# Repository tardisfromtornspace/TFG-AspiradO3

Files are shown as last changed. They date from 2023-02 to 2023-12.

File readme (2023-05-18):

Proyecto AspiradO3

Nuestro sistema está propuesto para limpiar la troposfera de sustancias químicas nocivas, principalmente el ozono troposférico, pero con unas simples modificaciones también de otros agentes contaminantes como el óxido nitroso, monóxido de carbono y partículas en suspensión, de acuerdo a las ODS 2 (Salud) y 13 (Acción por el clima).
Para ello, según nuestro plan inicial, utilizaríamos un sistema similar a un dirigible o globo aerostático, en el que los sistemas de control y actuación de nuestro dron estarían suspendidos por un globo de un gas ligero, helio o hidrógeno. Esto es para poder llegar a las áreas donde el ozono troposférico se encuentre, y donde un simple filtro a nivel del suelo no pudiera ayudar. El concepto funcionaría de forma similar a una aspiradora, en la que un motor propulsa el aire a través de una serie de filtros que eliminan el gas contaminante, utilizando un filtro de carbón activo, más un par de filtros anti-pájaro y HVAC (no está de más limpiar un poco la atmósfera de polución, ni evitar que nuestro filtro para ozono reaccione con otras sustancias no deseadas), y posiblemente un filtro catabólico selectivo de NOX basado en urea.

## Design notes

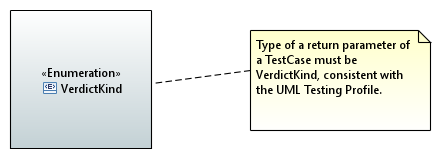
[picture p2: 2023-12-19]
Auxiliar/Papyrus/Test/Requirements_VerdictKind_Diagram.PNG

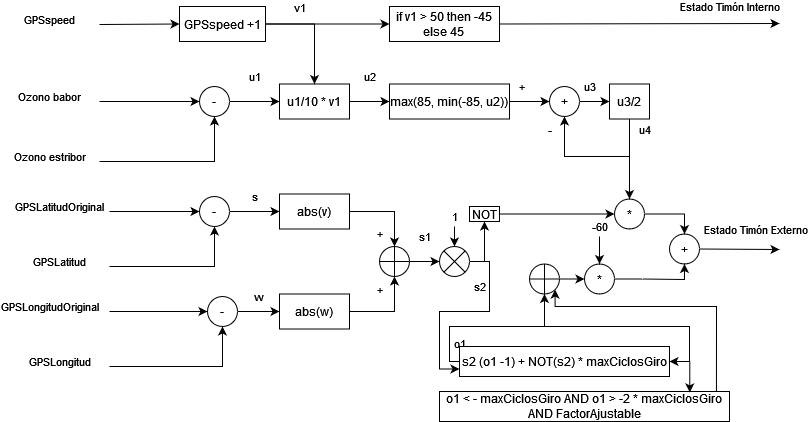
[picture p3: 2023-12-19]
Auxiliar/DiagramaSistemaControlSimple.png

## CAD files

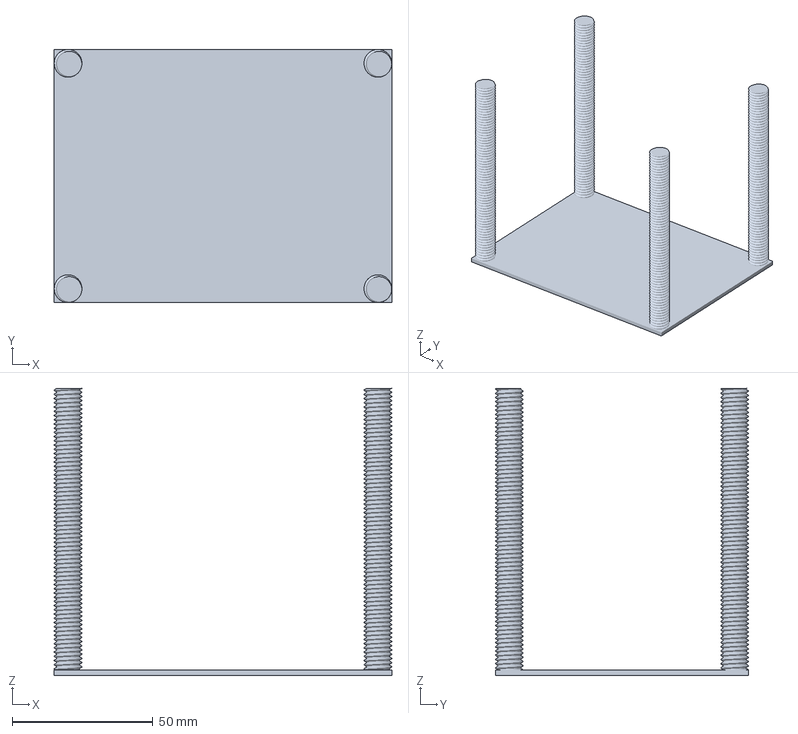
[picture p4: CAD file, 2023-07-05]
Chasis3D/main_structure.3mf
120.0 x 90.0 x 102.0 mm

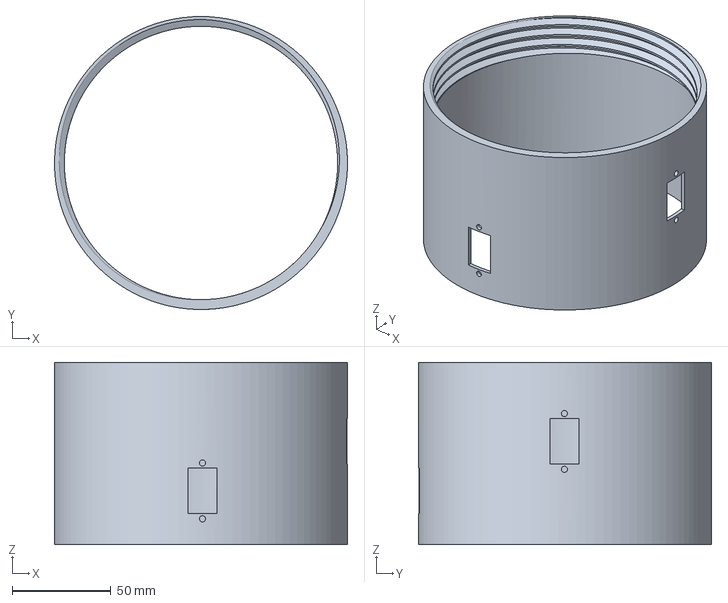
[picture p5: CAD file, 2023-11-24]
Chasis3D/CE3E3V2_tapa-trasera.3mf
148.0 x 148.0 x 92.0 mm

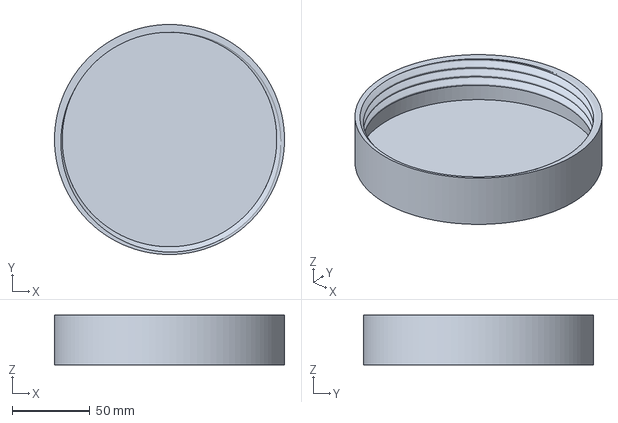
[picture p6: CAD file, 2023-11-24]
Chasis3D/CE3E3V2_tapas1y2.3mf
148.0 x 148.0 x 32.0 mm

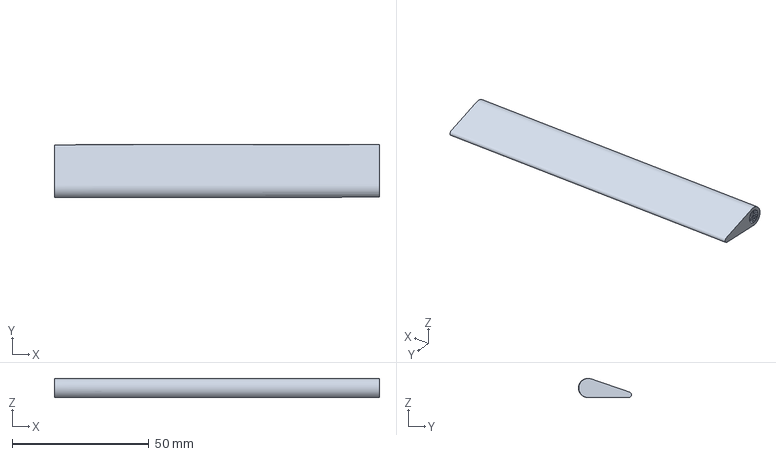
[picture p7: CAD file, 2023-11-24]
Chasis3D/CE3E3V2_timon_2.3mf
118.8 x 19.4 x 7.04 mm

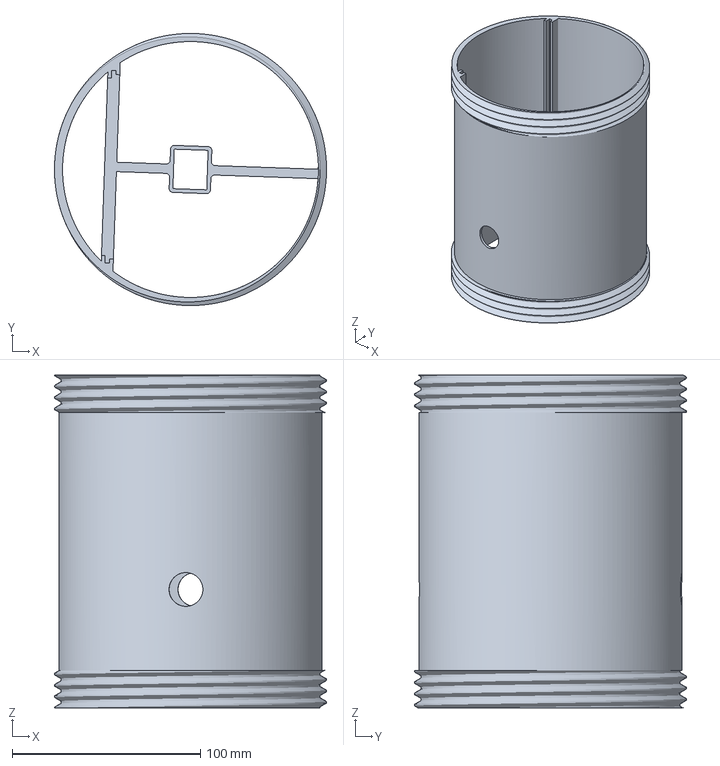
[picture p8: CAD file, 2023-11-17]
Chasis3D/CE3E3V2_chasis.3mf
144.6 x 144.6 x 177.0 mm

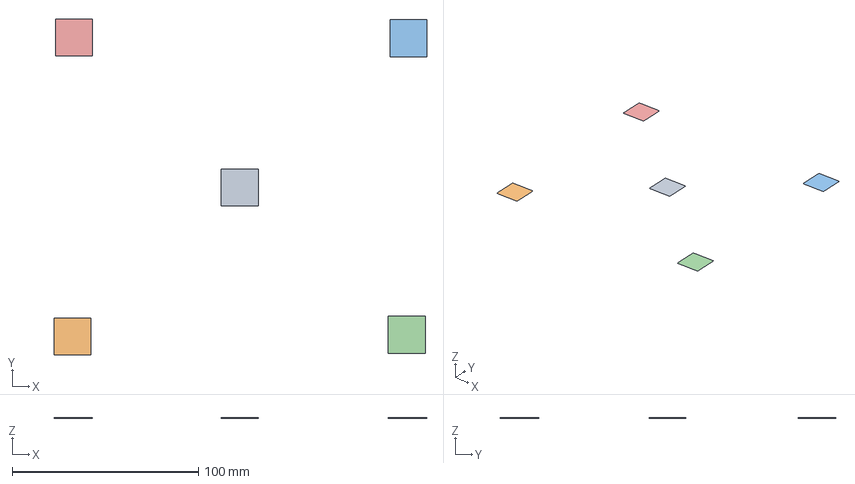
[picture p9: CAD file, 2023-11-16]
Chasis3D/CE3E3V2_Unnamed-Cubo5-PruebaEnder.3mf
200.3 x 180.4 x 0.4 mm
Unnamed-Cubo-PruebaEnder.stl
Unnamed-Cubo-PruebaEnder.stl(1)
Unnamed-Cubo-PruebaEnder.stl(2)
Unnamed-Cubo-PruebaEnder.stl(3)
Unnamed-Cubo-PruebaEnder.stl(4)

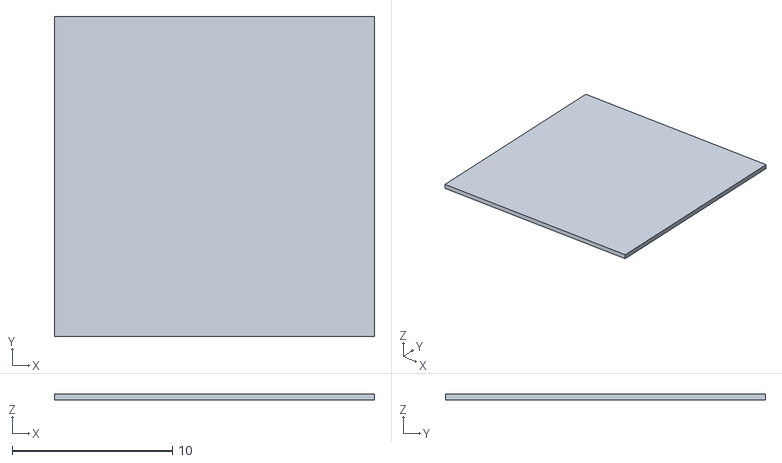
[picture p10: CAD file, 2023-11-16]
Chasis3D/Unnamed-Cubo-PruebaEnder.stl
20.0 x 20.0 x 0.4

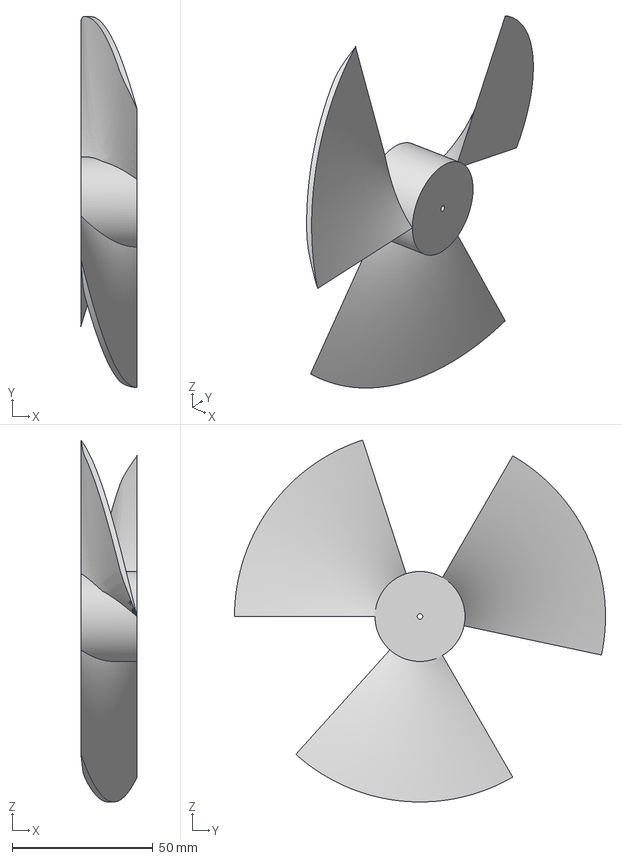
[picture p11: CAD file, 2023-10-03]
Chasis3D/helize.3mf
20.0 x 132.0 x 128.8 mm

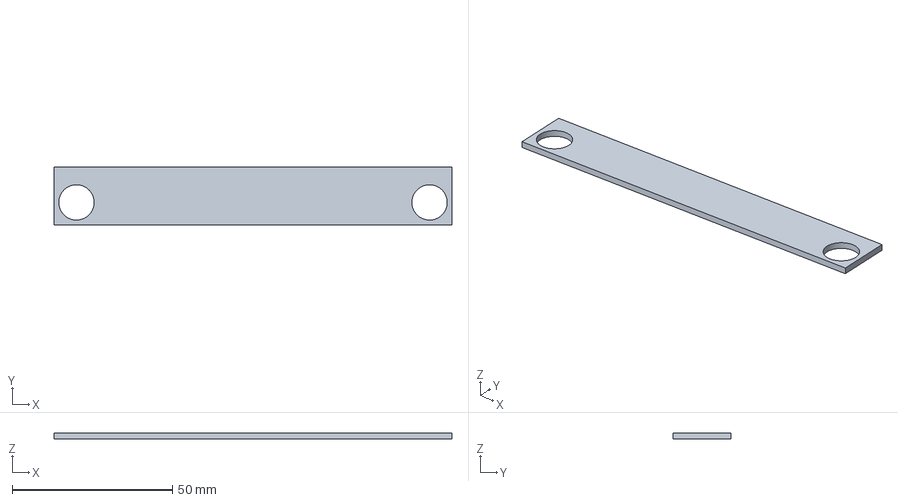
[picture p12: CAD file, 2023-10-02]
Chasis3D/ASX1_Cuerpo17AbrazaderasSoporte.3mf
124.0 x 18.0 x 2.00 mm

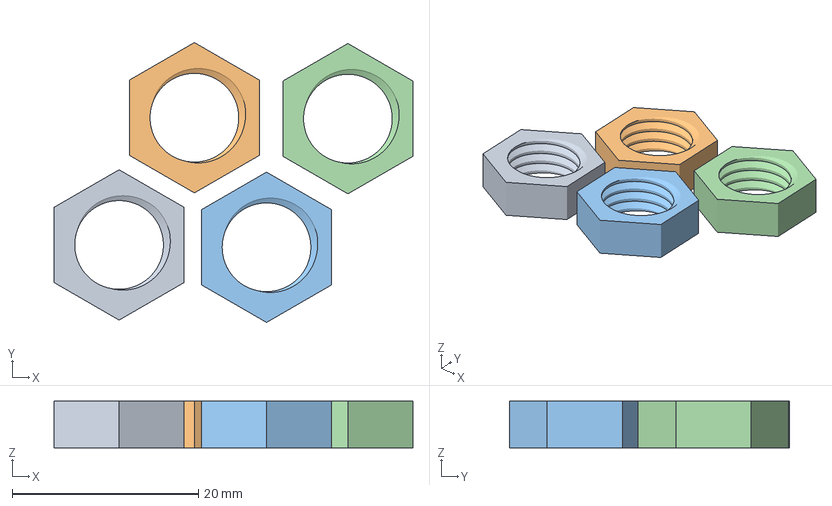
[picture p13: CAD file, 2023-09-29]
Chasis3D/These_nuts_4.3mf
38.6 x 30.1 x 5.00 mm
nut.3mf
nut.3mf(1)
nut.3mf(2)
nut.3mf(3)

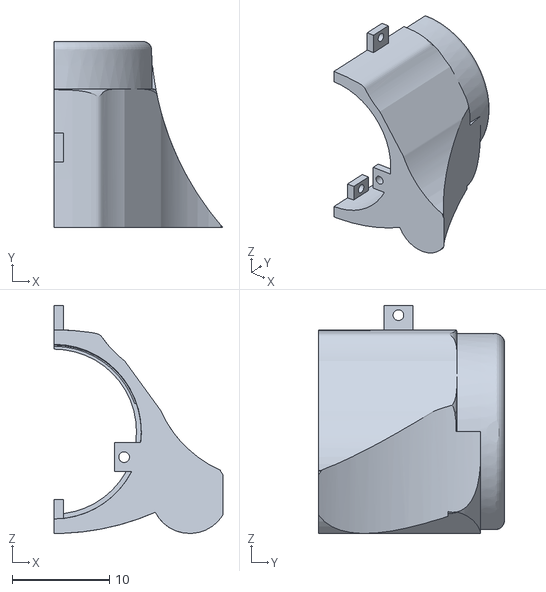
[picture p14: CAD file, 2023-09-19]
Chasis3D/ChasisBI_v3pto2-PROPUESTA.stl
17.4 x 19.2 x 23.5

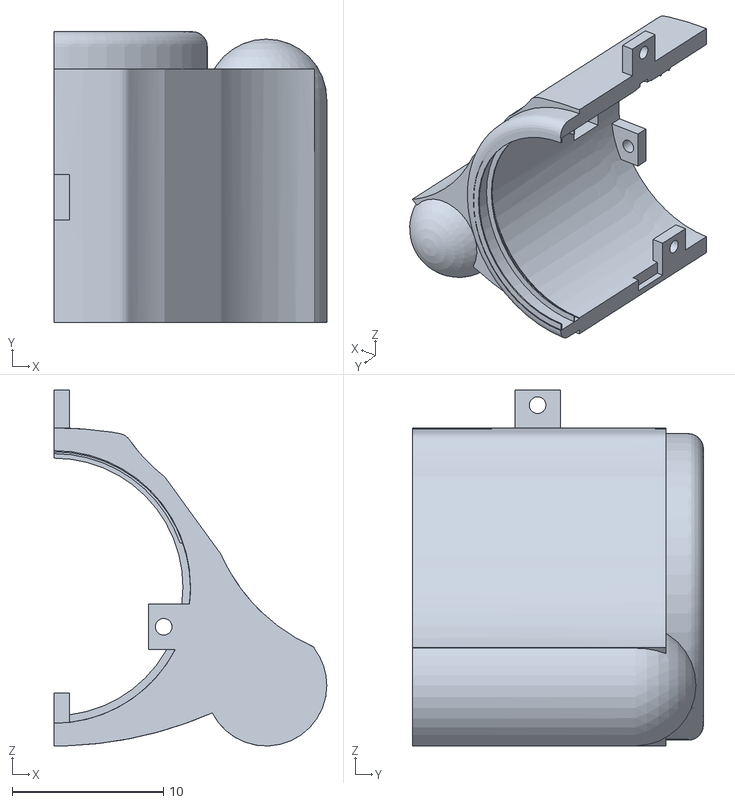
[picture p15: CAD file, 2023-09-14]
Chasis3D/ChasisBD-v3pto1.stl
18.0 x 19.2 x 23.5

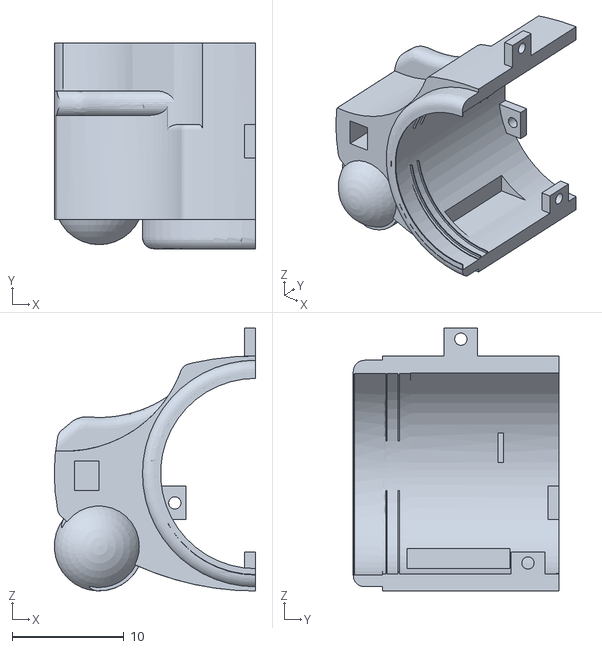
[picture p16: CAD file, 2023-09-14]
Chasis3D/ChasisFD-v3pto1.stl
18.0 x 18.4 x 23.5

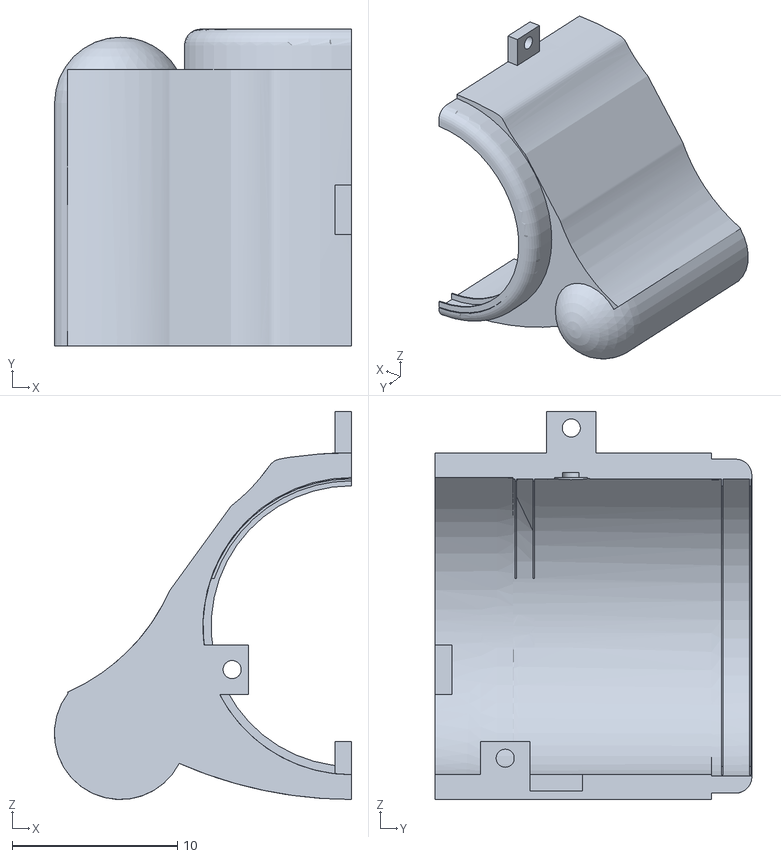
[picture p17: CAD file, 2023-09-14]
Chasis3D/ChasisBI-v3pto1.stl
18.0 x 19.2 x 23.5

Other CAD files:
Chasis3D/ASX1_soporte_main_structure.3mf
Chasis3D/Cuerpo17.3mf
Chasis3D/ChasisBD_v3pto2-PROPUESTA.stl
Chasis3D/ChasisFI-v3pto1.stl
Chasis3D/ASX1_Chasis-PrincipalBDreajustado.3mf
Chasis3D/ASX1_Chasis-PrincipalBIreajustado.3mf
Chasis3D/ASX1_Chasis-PrincipalBackD.3mf
Chasis3D/ASX1_Chasis-PrincipalBackI.3mf
Chasis3D/ASX1_Chasis-PrincipalFDRecalculado.3mf
Chasis3D/ASX1_Chasis-PrincipalFI.3mf
Chasis3D/ASX1_Chasis-PrincipalFIRecalculado.3mf
Chasis3D/ASX1_ChasisMisc.3mf
Chasis3D/ASX1_soporte_pinzas_tuercas.3mf
Chasis3D/Chasis-PrincipalBDreajustado.stl
Chasis3D/Chasis-PrincipalBIreajustado.stl
Chasis3D/Chasis-PrincipalBackD.stl
Chasis3D/Chasis-PrincipalBackI.stl
Chasis3D/Chasis-PrincipalFD.stl
Chasis3D/Chasis-PrincipalFDRecalculado.stl
Chasis3D/Chasis-PrincipalFI.stl
Chasis3D/Chasis-PrincipalFIRecalculado.stl
Chasis3D/Chasis.FCStd
Chasis3D/Chasis.stl
Chasis3D/ChasisMisc.stl
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

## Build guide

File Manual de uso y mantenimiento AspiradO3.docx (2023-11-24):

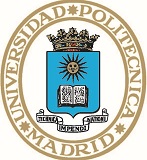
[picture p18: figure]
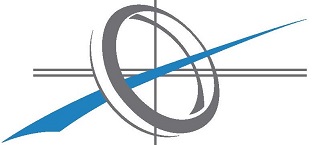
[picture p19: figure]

| Grado Ingeniería de Computadores
Universidad Politécnica de Madrid | | Escuela Técnica Superior de Ingeniería de Sistemas Informáticos

# PROYECTO FINAL DE GRADO

Proyecto Aspiradora de Ozono (AspiradO3)

Manual de uso y mantenimiento

Nombre del equipo: SBC22-M-01-AO3

https://upm365.sharepoint.com/:f:/s/SBC22M01/EjDevVEETKdIlYgdh2tLhi4BIAjwwNGaQKtBlmzocavBRA?e=Ovh6e4

Miembros del equipo:

Líder | Alumno | correo
X | Serrano López, Alejandro | alejandro.serranol@alumnos.upm.es

## DATOS DEL PROYECTO

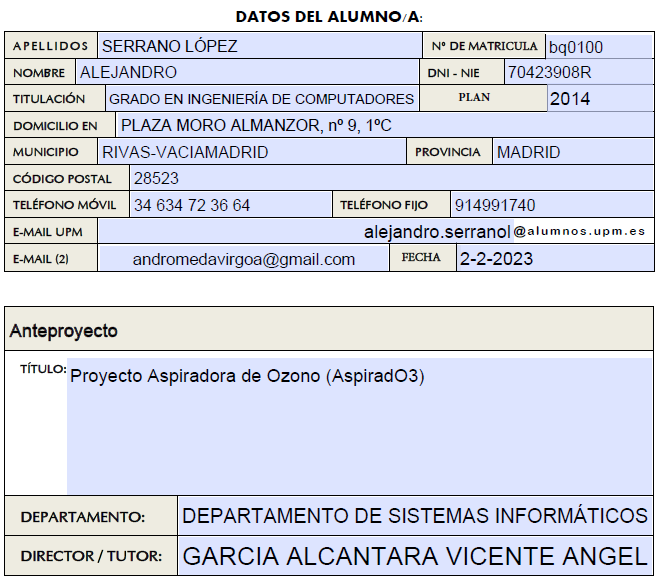
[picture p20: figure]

Co-tutor: Alberto Cruz (alberto.cruz@upm.es).

Índice

0. Introducción 4

1. Manual de uso : 5

2. Manual de mantenimiento : 10

3. Contacto : 13

4. Listado de materiales: 14

5. Referencias: 18

0. Introducción:

Este manual de uso y mantenimiento tiene como papel asegurarse de una correcta manipulación del dispositivo AspiradO3 durante la exposición, así como mantenerlo en las condiciones óptimas para su funcionamiento durante ésta, de acuerdo a lo presentado en los requisitos para las ayudas de TFG y TFM subsección Hardware (Yagüe Panadero, 2023).

Aunque finalmente dicha beca no fue aceptada para este proyecto y el prototipo no pudo ser terminado, se decidió mantener este manual para un uso más sencillo del prototipo a cara de presentaciones del proyecto.

1. Manual de uso:

AspiradO3 es un dispositivo aspirador aerostático incompleto que se dedicaría a detectar las regiones con mayor concentración de ozono troposférico para dirigirse a ellas y filtrarlo, reduciendo los potenciales problemas de salud.

Debido a como el autor de este documento está interesado en que su sistema se pruebe y todos lo puedan utilizar, dependiendo de en cuál fase de desarrollo se encuentren, deberán seguir más o menos fases de uso y construcción.

Por ejemplo, si se encuentran en la fase de construcción, es probable que tengan que pedir a alguna compañía que les produzca el PCB o el Chasis (a continuación en este link se les proporciona acceso al GitHub del proyecto para tener los esquemáticos de ambos listos, en el caso de los PCB todos los ficheros acabados en .gbr bajo la carpeta “Esquematicos\CircuiteriaESP32”, y el chasis en la carpeta “Chasis3D” los ficheros “…Reajustado.3mf” y “…Recalculado.3mf” para Ultimaker Cura y los ficheros .gcode bajo el zip “Chasis3D” o alternativamente una versión más ligera de 3 piezas enroscables, 2 timones, 1 aspa y soporte en formato .3mf (para la tapa delantera de la opción de no imprimir bordes superior e inferior para obtener la estructura de reja) bajo el fichero “Chasis3DV2” (Serrano López, 2023)). Se recuerda que el Chasis FreeCad está a escala 1:10, y a escala real en Ultimaker Cura, por lo que la impresión llevará su tiempo. Se recomienda el uso de plástico PLA por ser el menos nocivo entre las opciones disponibles en el momento de creación de este documento.

Las piezas deberán encajarse entre sí y adherirse adecuadamente, en el primer chasis puede ser necesario el pegamento de maqueta, aunque esta opción suponga inconvenientes a la hora de hacer el mantenimiento del dispositivo, mientras que en el segundo el sistema cuenta con piezas enroscables entre sí, para prescindir de esto y poder realizar un mantenimiento menos complicado. Se recuerda que si quieren usar tornillos externos deberán o bien usar el método de la tuerca caliente para hacer un agujero estable donde introducir el tornillo más tarde (por ejemplo utilizando un soldador para calentar la tuerca) o modificar el FreeCad para sus propios diseños. Una vez tengan las piezas del chasis y tras adquirir el globo de polietileno de suficientes litros para levantar el chasis (unos 2439 L para el primer chasis, 879 L para el segundo, según la fórmula aproximada de 1.025 g/L de empuje (Kazemi, 2022)), procedan a introducir la placa solar, antena GSM/GPS, sensores de ozono y circuitería en los lugares indicados, asegurándose de que los cables pueden llegar a la placa situada en el soporte (bajo el tabique horizontal en el primer chasis, en la cámara de aire en el segundo), antes del timón externo (ver Croquis del Sistema); que la placa solar se localiza sobre el globo, mirando hacia arriba, que los servomotores están en su posición correcta para que los timones encajen en sus respectivos ejes, perpendiculares al radio del tubo, y que los sensores de ozono externo estén mirándose hacia lados opuestos el uno del otro.

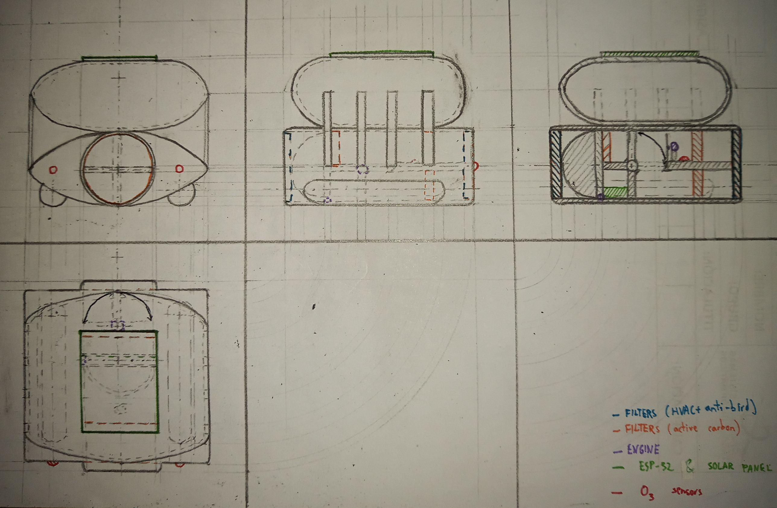
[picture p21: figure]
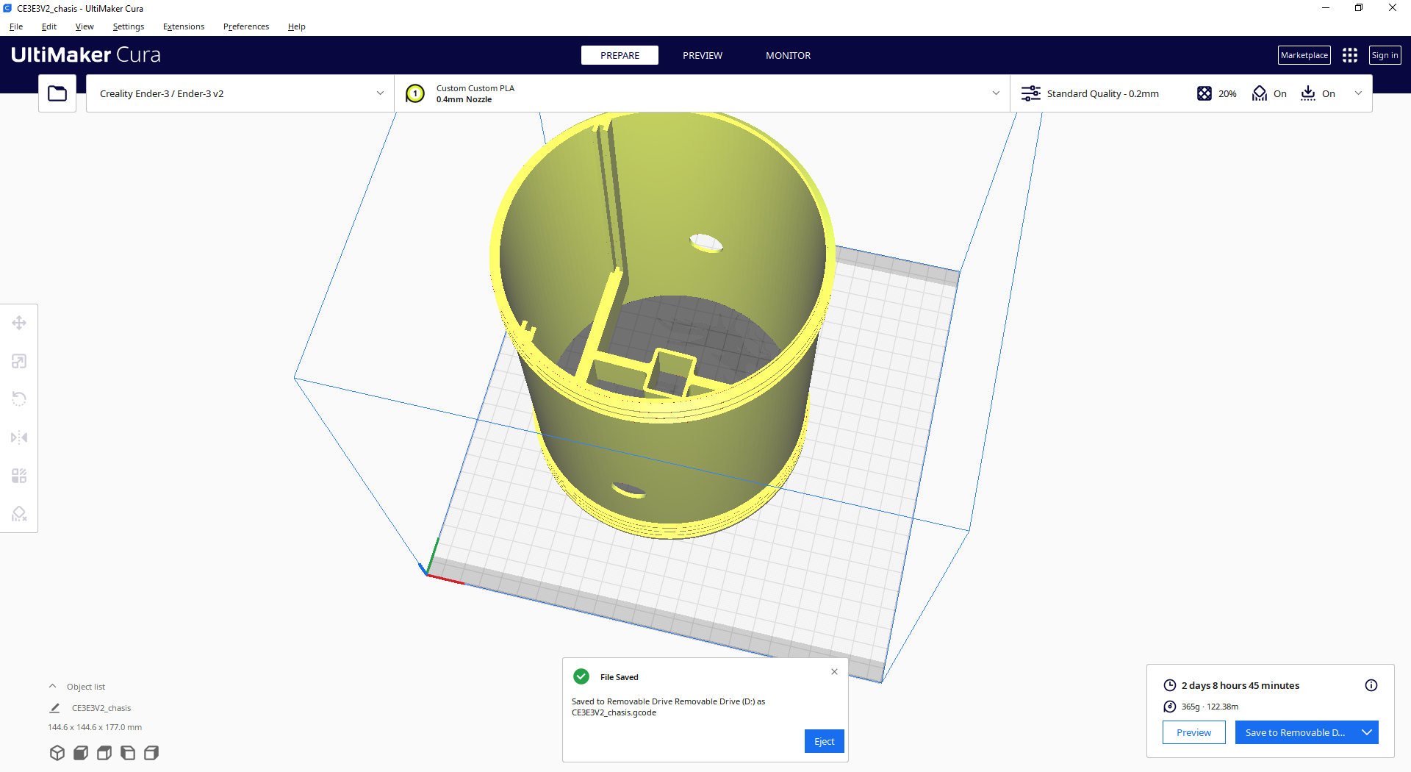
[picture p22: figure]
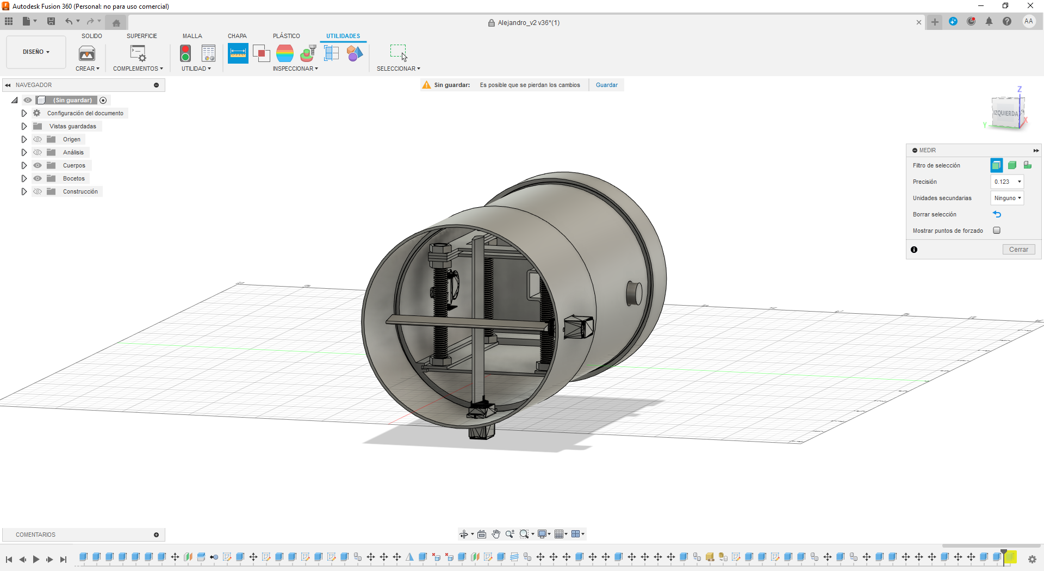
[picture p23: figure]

Figuras 1, 2 y 3: croquis del sistema + imágenes del chasis V2 – nótese que en el croquis hay un par de diferencias con el diseño del chasis V1 final, y es que la placa PCB se apoyará en dos de las baterías de litio Varta el el hueco del tabique bajo las aspas, y que el motor del timón interno se encuentra en el lado izquierdo y no el derecho; mientras que en el segundo chasis todo este soporte está en una pieza única que se puede encajar y desencajar del centro del chasis por deslizamiento y por debajo se situaría el sensor de ozono interno; y las ranuras circulares laterales es dónde se situarán los sensores de ozono externos (elaboración propia).

También necesitarán de una tarjeta SIM cargada y válida 4G, recomendamos una tarjeta de prepago para evitar sobrecostes, además de ser más barata. Nosotros empleamos una tarjeta de Lowi, bajo el servicio de Vodafone. El uso de dicha tarjeta SIM requerirá de la modificación del fichero sdkconfig para incluir el PIN (alterar la línea “CONFIG_MIPIN”). La utilización de otra compañía supondrá modificaciones adicionales a dicho sdkconfig, para indicar otra APN (“CONFIG_MIAPN”).

Para la conexión wi-fi, también requerirán de un punto de acceso wi-fi correcto – pueden bien utilizar los valores por defecto del sdkconfig y crear una red wifi con mismas credenciales (ver dos líneas de abajo) o bien modificar dichas líneas a las de un punto de acceso ya existente.

CONFIG_EXAMPLE_WIFI_SSID="SBC"

CONFIG_EXAMPLE_WIFI_PASSWORD="SBCwifi$"

Finalmente, para ver sus lecturas, se debe tener acceso al panel de Thingsboard (ver Referencias). Para el prototipo en sí no es necesario, pero para versiones a mayor escala se requerirán de modificaciones adicionales para modificar el token mqtt, de nuevo en sdkconfig:

CONFIG_MITOKENMQTT="YSRNEFDXnyIGhX9OaylG"

El uso del sistema tras esto es bastante sencillo. Antes de todo para una máxima eficiencia, se recomienda encarecidamente que se carguen las tres baterías encargadas del funcionamiento del dispositivo. Para ello se recomienda su extracción del dispositivo para una mejor manipulación, salvo la del sistema GPS/GSM, que utiliza parte de los sistemas de regulación de dicho componente para prevenir sobrecargas y dispone de uno de los puertos JST dicho módulo para permitir cargas externas, y por lo tanto debe mantenerse conectado a este módulo durante la carga. Todas las baterías utilizadas emplean un conector USB Micro para cargar y pueden aceptar hasta 5V y 2A de entrada, así que se requiere de un cable de carga/cargador que soporte dichas especificaciones. En el caso de las baterías Powerbank de 5V (tanto VARTA como gembird) se esperará hasta que todas las luces de dichas baterías brillen azul, mientras que con la de litio del GSM se esperará a que brillen los ledes naranja y verde de dicho módulo, que según el manual del GSM indican carga completa (ada, 2016). Por seguridad dicha carga se hará con la tarjeta SIM retirada. Si se utiliza la alternativa de 1 batería de 7.4V 5.2 Ah, deberá incorporarse el adaptador adecuado (ver listado de materiales) de tal forma que el OUT de cada adaptador se conecte a los zócalos de batería principal y los IN estén conectados a los polos correctos de la batería, según el manual de dicho adaptador (Future Electronics, 2023). Por favor, téngase en cuenta que si se utiliza esta opción no solo será algo más cara, sino que limitará considerablemente la capacidad de recarga que el panel solar proporciona a la batería principal y requerirá de un cargador especializado con balanceador de carga, como el fullwat cli1000 (Electronica Embajadores, 2023).

Una vez están todas las baterías cargadas se procederá a su conexión, de tal forma que las baterías VARTA estén conectadas por su USB tipo A de 5V 2.0A a sus correspondientes circuitos. Por como son baterías idénticas, su uso entre los dos USBs es indistinto. Una vez estén conectadas la ESP-32 comenzará a funcionar y una vez haya encontrado un wi-fi inicial procederá a una fase de calibración de los sensores de ozono, en la que tomará el valor más estable como referencia. Un detalle importante que notar sobre la calibración es que es más fiable cuánto más tiempo hayan estado encendidos los sensores Ozone3, puesto que su naturaleza electroquímica supone un tiempo de calentamiento que puede arrojar valores inestables. Es por estos dos motivos que durante dicha fase se recomienda estar en un ambiente controlado para que las mediciones posteriores sean lo más precisas posibles. Existe la opción de ver por UART el proceso conectando un cable adaptador USB Mico-USB a un ordenador o sistema que acepte UART directamente a la ESP-32, aunque por como el sistema está diseñado se recomienda simplemente esperar a que se reciban los primeros datos a la plataforma Thingsboard para observar el correcto funcionamiento del sistema. El programa está diseñado para no avanzar más a menos que encuentre la red wi-fi válida inicial a modo de prevenir problemas de calibración y consumo de datos móviles accidentales en caso de almacenamiento indebido, por ejemplo. Una vez se ha conectado a dicha red wi-fi, ya no es necesaria y podrá funcionar mediante la red móvil.

Una vez la calibración está completa se puede soltar el globo, transmitirá su localización a intervalos regulares así como su posición, orientación, lecturas de ozono, temperatura, humedad y luz, e irá navegando automáticamente en la dirección en la que detecte mayor cantidad de ozono. En el prototipo, los sensores electroquímicos usados se acostumbran a niveles de ozono cuando pasa suficiente tiempo, por lo que no pueden utilizarse para medir concentraciones exactas de ozono, sino subidas y descensos. Cabe notar que el paso de red Wi-fi a GSM puede tardar un poco, por lo que se insta que la primera vez al lanzarlo en una zona remota tras desconectar el Wi-Fi se espere a que transmita los datos al Thingsboard al menos una vez.

En el prototipo, incluso si se llegase a imprimir el chasis, la recogida actual del dispositivo es manual. Se recomienda el uso de un cordel o similar para evitar que vaya fuera del área designada. En versiones futuras se planea modificar esto para que tras cierto tiempo o tras alejarse demasiado vuelva al punto de origen.

2. Manual de mantenimiento:

Nuestro sistema está propuesto para limpiar la troposfera de sustancias químicas nocivas, principalmente el ozono troposférico, pero con unas simples modificaciones también de otros agentes contaminantes como el óxido nitroso, monóxido de carbono y partículas en suspensión, de acuerdo a las ODS 2 (Salud) y 13 (Acción por el clima). Es por ello que para un correcto funcionamiento el sistema debe mantenerse en prístinas condiciones.

Uno de los componentes vitales y más evidentes a mantener para el correcto mantenimiento del sistema son los filtros. Como muchos componentes, el efecto del tiempo así como su papel los desgasta hasta volverlos ineficientes. El papel de los filtros HVAC y anti-pájaro es reducir el impacto de esto sobre los filtros de carbón activo, especialmente de objetos extraños y algunas sustancias indeseadas. Otro son los sensores de ozono, que se utilizan tanto para la navegación como la monitorización del estado de los filtros, cuyo reemplazo es notablemente más costoso. En caso de que pase el período de vida medio de los filtros (3-6 meses para los filtros de carbón activo simples (Elica shop, 2023), y cada 30 días para los HVAC si se usan de forma regular, si no cada 3-6 meses (DM HVAC Refrigeration, 2021)) o que los sensores de ozono indiquen poca diferencia en los valores de ozono antes y tras el filtro de carbono activo, se deben reemplazar los filtros así como comprobar el estado de los sensores, puesto que los sensores electroquímicos también tienden a degradarse frente a sustancias químicas con el paso del tiempo y exposición a agentes atmosféricos y condiciones meteorológicas adversas. Se pueden usar filtros más avanzadas con un período de vida medio mayor siempre y cuando encajen en los espacios de los filtros (arco de circunferencia de 18.3 cm de diámetro, 8.5 cm de alto, 18.5 cm de ancho, 1 cm de grosor para los filtros de carbono activo, circulares de 18.34 cm de diámetro para los HVAC) y se sigan sus correspondientes procedimientos de lavado y regeneración de forma regular.

Cuando se realice el reemplazo de los filtros es recomendable aprovechar para limpiar los espacios de aspiración, que a pesar de los filtros podrían presentar suciedad que interfiera con otros componentes, como las aspas de los motores.

Otro componente a mantener es el dirigible que lo ayuda a mantenerse a flote. Antes de cada lanzamiento y tras cada recogida debe comprobarse que no hay pinchazos ni fugas, ya que reduciría considerablemente el tempo de vuelo útil. En caso de detectarse fugas se recomienda parcharlas (o si no es posible, reemplazar el globo) y reinflar el dirigible con Helio.

El módulo GSM requiere de un gran consumo energético, por lo que deben asegurarse de que la batería de litio dedicada al módulo esté conectada y suficientemente cargada inicialmente como para no drenar los otros sistemas, si no la espera para que el panel solar la cargue será muy larga. El pmod GPS también consume, aunque considerablemente menos, y es bastante sensible a variaciones de voltaje. Debido a como ambos módulos siguen consumiendo energía incluso cuando el resto del sistema esté apagado, se recomienda desconectar las baterías para asegurarse que tras un tiempo prolongado éstas mantienen la carga.

En caso de rotura del cable de la antena o de otros componentes, deberá reemplazarse de acuerdo con la lista de materiales indicada en la sección 4 de este documento. En el caso de un chasis roto, se recomienda seguir las indicaciones de la fase construcción del apartado anterior, asegurándose que se retiran los filtros primero, posteriormente las baterías y generadores (como la placa solar), para seguirles la PCB, los servos, motores y sensores. Si se usó el pegamento de maqueta, es posible que a menos que se tenga cuidado, se deba reemplazar el chasis entero. En caso contrario bastará con remover/desatornillar la parte dañada y reimprimirla, con un menor gasto de tiempo y recursos. Este último caso es aplicable a las aspas y timones, de cualquier modo, aunque se deberán imprimir en ficheros por separado para evitar reimprimir partes no dañadas.

En la segunda versión del chasis se puede desenroscar la tapa frontal para permitir una manipulación de los filtros delanteros, del motor aspirador y superficial de la circuitería; mientras que desenroscar la tapa trasera permitirá acceder a los filtros traseros, el soporte de la circuitería, así como los servomotores – téngase en cuenta que la extracción por la tapa trasera puede conllevar la torsión de los cables de los servos si estos no han sido instalados con cuidado o se han separado de la placa PCB.

Una excepción a lo de arriba es la PCB, donde algunos errores menores de pista pueden ser apañados con un poco de soldadura o las herramientas adecuadas para remover malas conexiones.

Los servomotores y sensores de temperatura y humedad utilizados indicados en la sección 4 no requieren de un mantenimiento especial, aparte de revisarlos de forma periódica anual para revisar problemas. Sin embargo el motor de las aspas sí requiere de un mantenimiento contante tras cada uso puesto que en nuestro prototipo es un motor de escobillas y este tipo de motores tienden a desgastarlas frente a un uso continuo. En caso de daño a las escobillas este componente debe reemplazarse parcial- (por ejemplo las susodichas escobillas) o totalmente.

3. Contacto:

En caso de cualquier incidencia, contacte con el tutor encargado del Taller de Fin de Titulación asignado.

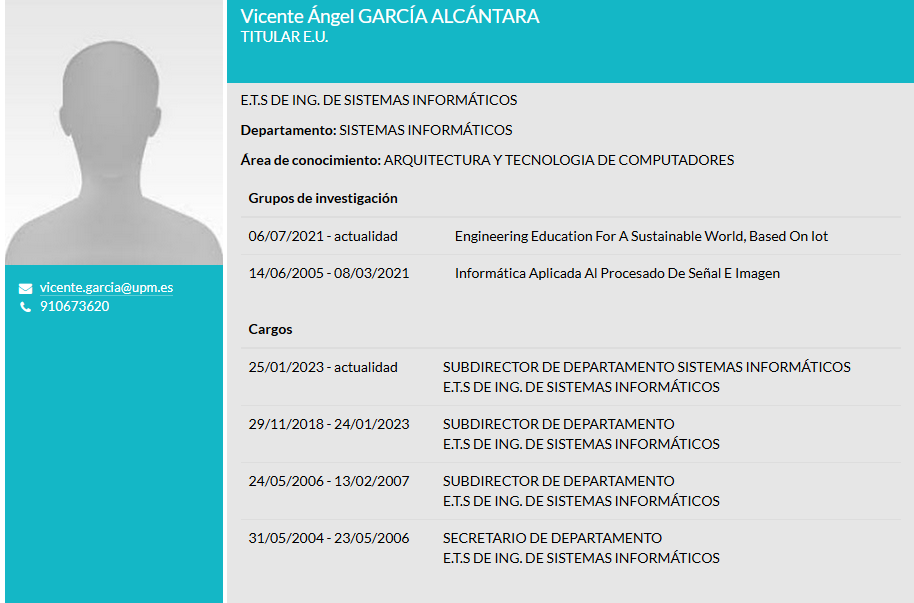
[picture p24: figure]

Figura 4: Captura de pantalla de portal de Transparencia sobre información de Contacto del Profesor Vicente García Alcántara (Portal de Transparencia UPM, 2023).

4. Listado de materiales:

Este listado de materiales se incorpora al manual para ayudar al usuario a encontrar reemplazos para los componentes.

Haríamos uso de impresión 3D para montar el chasis y los dos filtros anti-pájaros, por lo que no se cuentan en el precio. En caso de dudas contáctenos.

Los proveedores, se debe tener en cuenta de que solo se incluyen resultados de los proveedores indicados, aunque existan en otros (eso es, proveedor primario UPM es https://es.rs-online.com/web/ (https://es.rs-online.com/web/i) mientras que los proveedores alternativos (muy difícil que lleguen a tiempo) son https://www.mouser.es/, https://www.electronicaembajadores.com/, y https://www.az-delivery.de/es/ ) a menos que no se encuentre en ninguno de esos proveedores.

Para precios variables se toma la opción de mayor coste a la hora de calcular. Hay que indicar que algunos de dichos componentes pueden reemplazarse por opciones más baratas si fuese necesario, realizando algunas modificaciones al chasis. También se indican alternativas consideradas y utilizadas durante el diseño del proyecto que pudieran ser válidas (aunque más caras), dejándose su nombre y precio resaltados en gris, y no contándose en el precio final.

Tabla 1: Tabla de precios de nuestros componentes (Elaboración propia).

Componente | Proveedor primario | | Proveedor alternativo | Unidades | Precio sin IVA | Precio con IVA
| URL RS- online | Número de ref. RS | URL
Procesador ESP-32 AzDelivery | N/A | (NO RS) | https://www.az-delivery.de/en/products/esp32-developmentboard | 1 | 10,99 € | 10,99 €
MikroElektronika Ozone 2 Click–MIKROE-2767 | https://es.rs-online.com/web/p/kits-de-desarrollo-de-sensores/1651064 | 165-1064 | https://www.mouser.es/ProductDetail/Mikroe/MIKROE-2767?qs=1mbolxNpo8cHSPn6LrSrWQ%3D%3D | 3 | 46,66 * 3 € 42,30 * 3 € (mouser) | 56,46 * 3 € 51,19 * 3 € (mouser)
Módulo ADC Adafruit ADS1015 | https://es.rs-online.com/web/p/convertidores-analogico-digital/1977077 | 197-7077 | https://www.electronicaembajadores.com/es/Productos/Detalle/LCINAD4/modulos-electronicos/modulos-instrumentacion/ads1015-convertidor-analogico-digital-adc-4-canales-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 | 1 | 11.67 € (electronicaembajadores) | 14,12 € (electronicaembajadores)
Resistencias de 4k7 | https://es.rs-online.com/web/p/resistencias-de-montaje-en-orificio-pasante/7078280 | 707-8280 | - | 2 | 0.179. * 2 € | 0.217 *2 €
Condensador 220 µF | N/A | (NO RS) | https://www.electronicaembajadores.com/es/Productos/Detalle/COEL22725/condensadores/condensadores-electroliticos/condensador-electrolitico-radial-220-uf-25-v-105-c | 1 | 0.107 € | 0.13 €
Diodos rectificadores 1N4007 | N/A | (NO RS) | https://www.electronicaembajadores.com/es/Productos/Detalle/SMDI1N4007/semiconductores/diodos-excepto-leds/1n4007-diodo-rectificador-1000-v-1-a | 2 | 0.115 € | 0.14 * 2€
Filtro de carbono activo | https://es.rs-online.com/web/p/accesorios-para-aspiradores-de-humo-de-soldadura/1234906 | 123-4906 (fabricado por RS) | (Más similar) https://www.mouser.es/ProductDetail/Metcal/FM-MSA25U?qs=rQFj71Wb1eXTSvMuYg2bpg%3D%3D | 1 | 9,86 € (bolsa de 3) 3,287 € (ud.) | 11,93 € (bolsa de 3)
Filtro HVAC | https://es.rs-online.com/web/p/filtros-de-aire-para-climatizacion/7302921 | 730-2921 (fabricado por RS) | No encontrado en proveedores alternativos | 1 | 41,28€ (pack de 10) 4,128 € (ud.) | 49,95 (pack de 10)
PowerBank 5V | https://es.rs-online.com/web/p/power-banks/2361454 | 236-1454 | https://www.electronicaembajadores.com/es/Productos/Detalle/BA70003/baterias-pilas-y-cargadores/power-bank/gembird-pb05-02-power-bank-5v-5000-ma | 2 | 17,80 * 2 € 9,85 * 2 (electronicaembajadores) | 21,54 * 2 € 11,91 * 2 € (electronicaembajadores)
Batería 7.4V 5.2Ah (alternativa a las 2 baterías de 5V, si no están disponibles) | https://es.rs-online.com/web/p/baterias-recargables/1449412 | 144-9412 | - | 1 | 38,04 | 46,03 €
Convertidor de corriente 5-40V a 5V 2A (si se usn baterías distintas a la PowerBank 5V) | N/A | NO RS | https://www.electronicaembajadores.com/es/Productos/Detalle/SA31375/sistemas-de-alimentacion/convertidores-dc-dc-uso-general/convertidor-dc-dc-in-4-5-40-v-out-5-v-2-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 | 1 | 4.96 € | 5,995 €
Cables conexión USB baterías a PCB | - | - | https://www.electronicaembajadores.com/es/Productos/Detalle/CX31041/conexiones/conexiones-usb-pc-multimedia/nanocable-cable-usb-2-0-usb-a-macho-a-micro-usb-b-macho-0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 (NOTA: requerirán de ser modificadas para la PCB, lo llameremos “modificar”) https://www.electronicaembajadores.com/es/Productos/Detalle/LCA1US4/modulos-electronicos/arduino/sparkfun-ftdi-cable-5v-cable-adaptador-dev-09718/ (versión para si no pueden modificar componentes demasiado, la llamaremos “intacto”) | 2 | 2,33 * 2 € (electronicaembajadores, modificar) 20,39 *2 € (electronicaembajadores, intacto) | 2,82 *2 € (electronicaembajadores, modificar) 24,68 * 2 € (electronicaembajadores, intacto)
Digilent Pmod GPS: GPS Receiver - 410-237 | https://es.rs-online.com/web/p/kits-de-desarrollo-de-sensores/1346455 | 134-6455 | https://www.mouser.es/ProductDetail/Digilent/410-237?qs=s%2FdyVPQMB4zUVDfMdmdUxQ%3D%3D | 1 | 43,97 € | 53,20 €
Placa Solar 6V | https://es.rs-online.com/web/p/paneles-solares/1860599 | 186-0599 | No encontrado - más similar: https://www.mouser.es/ProductDetail/Adafruit/3809?qs=MLItCLRbWswl2zZ4yMv4FA%3D%3D | 1 | 16,00 € | 19,36 €
Motores para aspas: Motor DC RS PRO, 1,5 → 3 V., 1,21 W, 8200 → 14000 rpm, par máx. 10,4 gcm, Ø de eje 2mm | https://es.rs-online.com/web/p/motores-dc/2389692 | 238-9692 | - | 1 | 2.48 € | 3 €
Puente H L9110S | https://es.rs-online.com/web/p/complementos-de-bbc-micro-bit/2153182 | 215-3182 | - | 1 | 1,07 € | 1,29 €
Motores para orientación : Servomotor SG-90 | https://es.rs-online.com/web/p/componentes-de-movimiento-para-robots-educativos/2153180 | 215-3180 | https://www.electronicaembajadores.com/es/Productos/Detalle/MMSV002/motores-servomotores-actuadores-lineales/servomotores/tower-pro-sg90-9g-servomotor-miniatura | 2 | 4,05 * 2 € 3,04 * 2 € (electronicaembajadores) | 4,90 * 2 € 3,68 * 2 € (electronicaembajadores)
Globo (Super-Pressure Balloon) | N/A | (NO RS) | No encontrado en proveedores alternativos. Más similares: https://www.amazon.es/ZERODECO-Decoraci%C3%B3n-cumplea%C3%B1os-Birthday-Accesorios/dp/B07KRXKD5Z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 https://www.amazon.es/Angry-Birds-AR-1013-Air-Swimmers/dp/B009YB3ICI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 ALTERNATIVA: Instrucciones de construcción https://www.instructables.com/RC-Zeppelin-dirigible/ | 1 | 18,33 € | 22,17 €
Helio | N/A | (NO RS) | No encontrado en proveedores alternativos. Más similar: https://www.donglobo.com/helio-para-globos/bombona-de-helio-para-globos-013m3-sin-globos | 1 | 24,72 € (bombona) | 29,90 € (bombona)
Módulo SIM800H para GPS y GSM | https://es.rs-online.com/web/p/kits-de-desarrollo-inalambricos-y-de-comunicacion/1245474 | 124-5474 | Más similar: https://www.mouser.es/ProductDetail/Mikroe/MIKROE-1720?qs=bzW4KIwE9U38mry2K8X5yA%3D%3D | 1 | 41,22 € | 49,88 € * *Puede que requiera de antena externa y microSD
Modulo de Expansión Diligent Pmod GPS: GPS Receiver | https://es.rs-online.com/web/p/kits-de-desarrollo-de-sensores/1346455 | 134-6455 | - | 1 | 30,05 € | 36.37 €
Antena SMA y adaptador para SIM800 | https://es.rs-online.com/web/p/antenas-gsm-y-gprs/7934376 | 793-4376 | Más similar: https://www.electronicaembajadores.com/es/Productos/Detalle/LCGS004/modulos-electronicos/modulos-gsm/sim800l-v2-0-modulo-gprs-gsm-850-900-1800-1900-mhz-antena-sma | 1 | 11,42€ | 13,82 €
Tarjeta SIM Móvil | - | - | - | 1 | - | Lowi 7,95 €/mes (incluye precio inicial)
Batería auxiliar para módulo SIM800H, LiPo 3.7V 2400 mAh | - | - | https://www.electronicaembajadores.com/es/Productos/Detalle/BA1A3724/baterias-pilas-y-cargadores/baterias-de-polimero-de-litio/bateria-de-polimero-litio-3-7-v-2400-m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 | 1 | 17.65 € | 21.36 €
Sensor de humedad y temperatura SHT85, 0.01 %RH, encapsulado 4 pines, interfaz Serie I2C. | https://es.rs-online.com/web/p/circuitos-integrados-de-sensores-de-temperatura-y-humedad/1826530 | 182-6530 | https://www.mouser.es/ProductDetail/Sensirion/SHT85?qs=byeeYqUIh0OExKWW1Eu%252BLQ%3D%3D | 1 | 47,31 € 31,38 € (mouser) | 57,25 € 37,97 € (mouser)
Fabricación PCB | | | | | | 11.24 € producción + 15,75 € de transporte (JLCPCB en Hong Kong)
TOTAL | | | | | | 645,109 €

5. Referencias:

Link del panel Thingsboard

https://demo.thingsboard.io/dashboard/fe483230-5512-11ed-b827-c9be76c6f5d7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

INDICE DE FIGURAS:

INDICE DE TABLAS:

REFERENCIAS:

ada, l. (28 de 9 de 2016). docs.rs-online.com. Obtenido de docs.rs-online.com: https://docs.rs-online.com/5a70/0900766b81533fcf.pdf

DM HVAC Refrigeration. (31 de 1 de 2021). www.dmhvacrefrigeration.com. Obtenido de www.dmhvacrefrigeration.com: https://www.dmhvacrefrigeration.com/es/mantenimiento-recambio-filtros-hvac/

Electronica Embajadores. (16 de 6 de 2023). www.electronicaembajadores.com. Obtenido de www.electronicaembajadores.com: https://www.electronicaembajadores.com/es/Productos/Detalle/BA2A951/baterias-pilas-y-cargadores/cargadores-y-descargadores/fullwat-cli1000-cargador-basico-de-bateria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

Elica shop. (22 de 5 de 2023). www.elica.com. Obtenido de www.elica.com: https://www.elica.com/ES-es/magazine/guias/filtros-de-carbon-activado-de-la-campana-cuando-cambiarlos

Future Electronics. (14 de 6 de 2023). cdn.shopify.com. Obtenido de cdn.shopify.com: https://cdn.shopify.com/s/files/1/0672/9409/files/5-40_to_5v_dc_step_down_with_display_and_usb_charger-HW-318-v6.pdf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

Kazemi, P. (25 de 8 de 2022). https://purecalculators.com. Obtenido de https://purecalculators.com: https://purecalculators.com/es/helium-balloons-calculator

Portal de Transparencia UPM. (6 de 2 de 2023). https://transparencia.upm.es. Obtenido de https://transparencia.upm.es: https://transparencia.upm.es/personal/pdi/cv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

Serrano López, A. (30 de 5 de 2023). github.com. Obtenido de github.com: https://github.com/tardisfromtornspace/TFG-AspiradO3/tree/master

Yagüe Panadero, A. (18 de 1 de 2023). www.etsisi.upm.es. Obtenido de www.etsisi.upm.es: https://www.etsisi.upm.es/sites/default/files/programa_propio_etsisi_2023.pdf

Versión: 24/11/2023

PHR Pág. 2

PHR Pág. 3 PFA

PHR Pág. 4 PFA

AspiradO3 (manual de uso y mantenimiento)

Proyecto Aspiradora de Ozono (manual de uso y mantenimiento)

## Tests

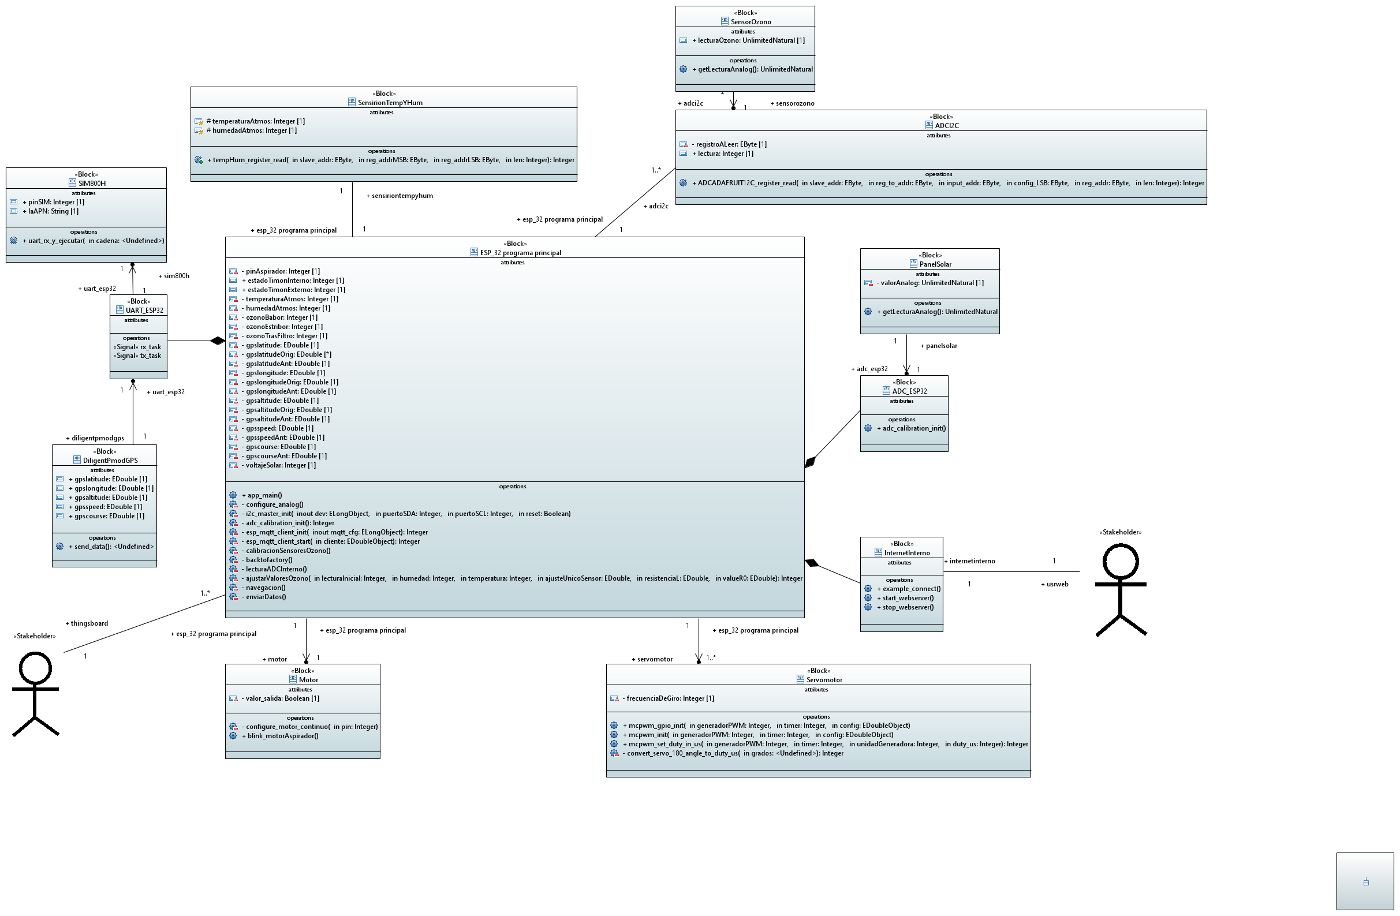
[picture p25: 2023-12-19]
Auxiliar/Papyrus/Test/SysML_1_6_Block_Definition_Diagram.PNG

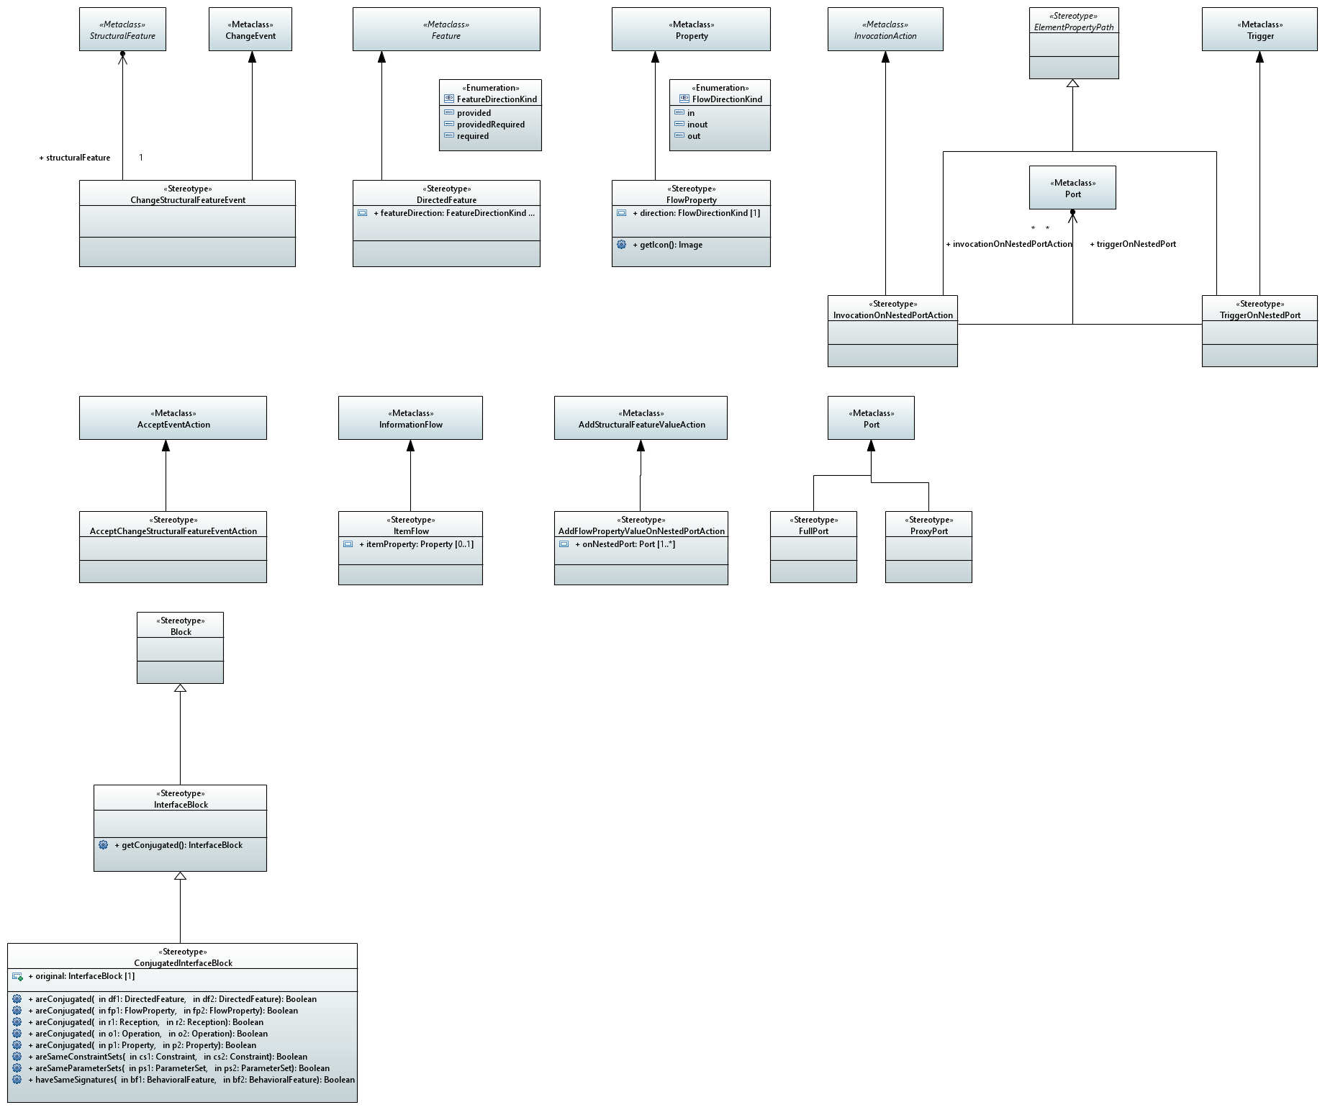
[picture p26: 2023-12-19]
Auxiliar/Papyrus/Test/PortsAndFlows.PNG

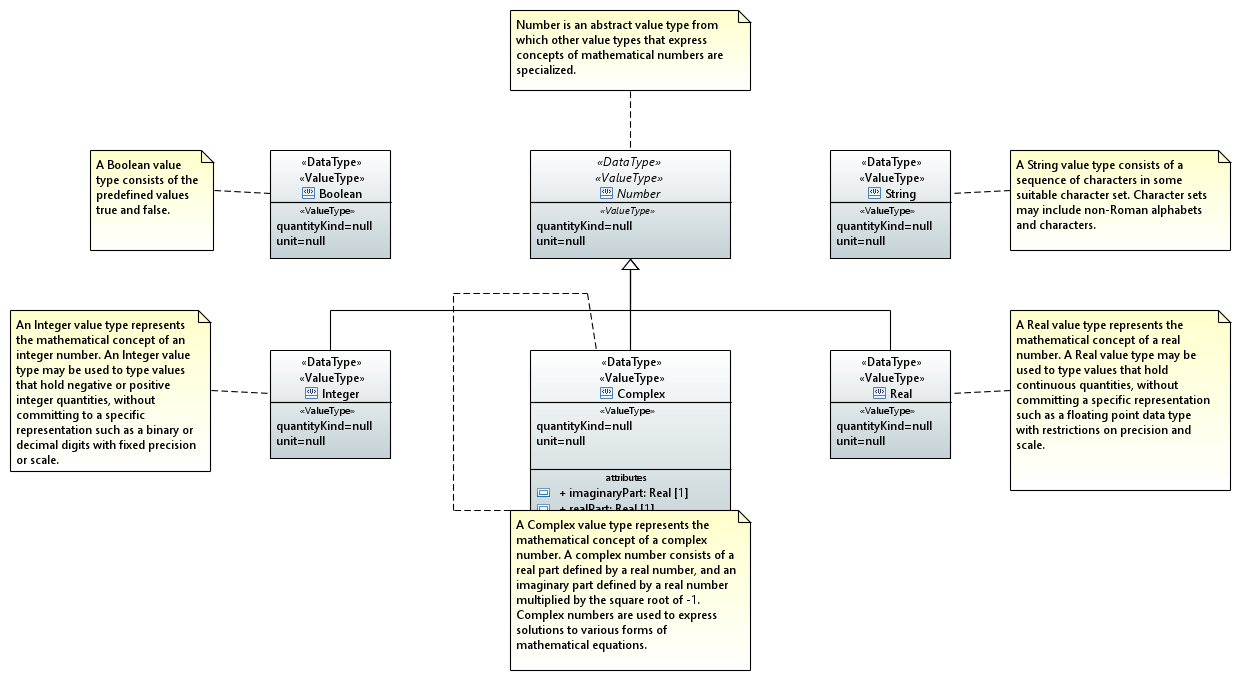
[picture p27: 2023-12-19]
Auxiliar/Papyrus/Test/Primitive_Value_Types_Diagram.PNG

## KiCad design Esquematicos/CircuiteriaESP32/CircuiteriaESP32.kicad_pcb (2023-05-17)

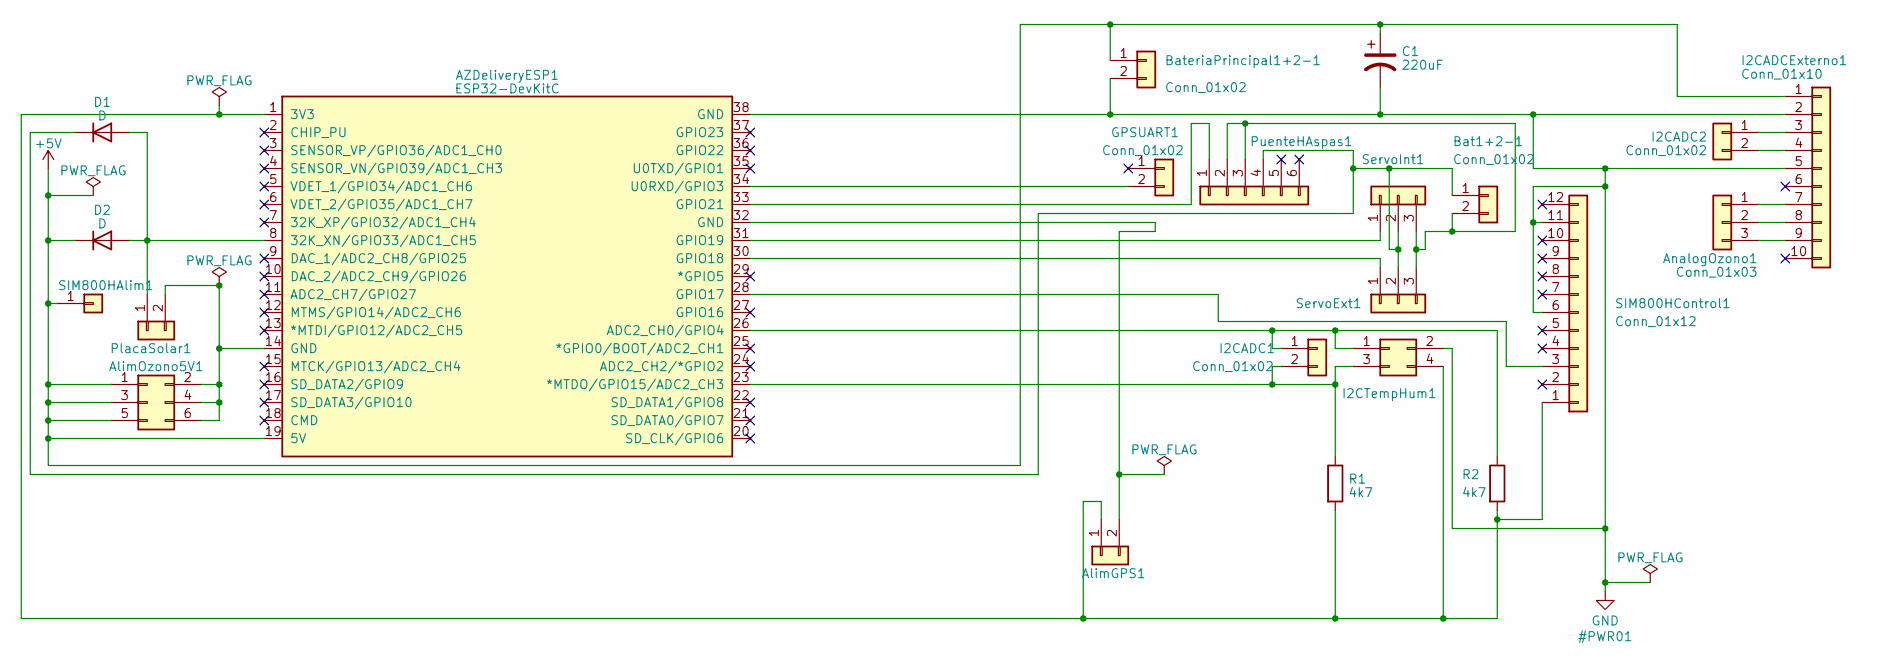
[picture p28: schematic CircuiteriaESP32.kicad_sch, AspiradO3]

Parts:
AZDeliveryESP1: ESP32-DevKitC
AlimGPS1: Conn_01x02; PinHeader_1x02_P2.54mm_Vertical
AlimOzono5V1: Conn_02x03_Odd_Even; PinHeader_2x03_P2.54mm_Vertical
AnalogOzono1: Conn_01x03; PinHeader_1x03_P2.54mm_Vertical
Bat1+2-1: Conn_01x02; PinHeader_1x02_P2.54mm_Vertical
BateriaPrincipal1+2-1: Conn_01x02; PinHeader_1x02_P2.54mm_Vertical
C1: 220uF; CP_Radial_D8.0mm_P3.50mm
D1, D2: D; D_T-1_P2.54mm_Vertical_AnodeUp
GPSUART1: Conn_01x02; PinHeader_1x02_P2.54mm_Vertical
I2CADC1, I2CADC2: Conn_01x02; PinHeader_1x02_P2.54mm_Vertical
I2CADCExterno1: Conn_01x10; PinHeader_1x10_P2.54mm_Vertical
I2CTempHum1: Conn_02x02_Odd_Even; PinHeader_2x02_P2.54mm_Vertical
PlacaSolar1: Conn_01x02; PinHeader_1x02_P2.54mm_Vertical
PuenteHAspas1: Conn_01x06; PinHeader_1x06_P2.54mm_Vertical
R1, R2: 4k7; R_Axial_DIN0204_L3.6mm_D1.6mm_P7.62mm_Horizontal
SIM800HAlim1: Conn_01x01; PinHeader_1x01_P2.54mm_Vertical
SIM800HControl1: Conn_01x12; PinHeader_1x12_P2.54mm_Vertical
ServoExt1: Conn_01x03; PinHeader_1x03_P2.54mm_Vertical
ServoInt1: Conn_01x03; PinHeader_1x03_P2.54mm_Vertical

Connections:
+5V: AZDeliveryESP1.19 (5V), AlimOzono5V1.1, AlimOzono5V1.3, AlimOzono5V1.5, BateriaPrincipal1+2-1.1, C1.1, D2.1 (K), I2CADCExterno1.1, SIM800HAlim1.1
GND: AZDeliveryESP1.38 (GND), BateriaPrincipal1+2-1.2, C1.2, I2CADCExterno1.2, I2CADCExterno1.5, I2CTempHum1.2, SIM800HControl1.6, SIM800HControl1.11
unnamed: AZDeliveryESP1.1 (3V3), AlimGPS1.1, I2CTempHum1.4, R1.2, R2.2, SIM800HControl1.1
unnamed: AZDeliveryESP1.8 (32K_XN/GPIO33/ADC1_CH5), D1.2 (A), D2.2 (A), PlacaSolar1.1
unnamed: AZDeliveryESP1.23 (*MTDO/GPIO15/ADC2_CH3), I2CADC1.2, I2CTempHum1.3, R1.1
unnamed: AZDeliveryESP1.26 (ADC2_CH0/GPIO4), I2CADC1.1, I2CTempHum1.1, R2.1
unnamed: AZDeliveryESP1.28 (GPIO17), SIM800HControl1.3
unnamed: AZDeliveryESP1.30 (GPIO18), ServoExt1.1
unnamed: AZDeliveryESP1.31 (GPIO19), ServoInt1.1
unnamed: AZDeliveryESP1.33 (GPIO21), PuenteHAspas1.1
unnamed 10: AZDeliveryESP1.34 (U0RXD/GPIO3), GPSUART1.2; also elsewhere on the board
unnamed: AZDeliveryESP1.32 (GND), AlimGPS1.2
unnamed: AZDeliveryESP1.14 (GND), AlimOzono5V1.2, AlimOzono5V1.4, AlimOzono5V1.6, PlacaSolar1.2
unnamed: AnalogOzono1.1, I2CADCExterno1.7
unnamed: AnalogOzono1.2, I2CADCExterno1.8
unnamed: AnalogOzono1.3, I2CADCExterno1.9
unnamed: Bat1+2-1.1, D1.1 (K), PuenteHAspas1.4, ServoExt1.2, ServoInt1.2
unnamed: Bat1+2-1.2, PuenteHAspas1.2, PuenteHAspas1.3, ServoExt1.3, ServoInt1.3
unnamed: I2CADC2.1, I2CADCExterno1.3
unnamed: I2CADC2.2, I2CADCExterno1.4

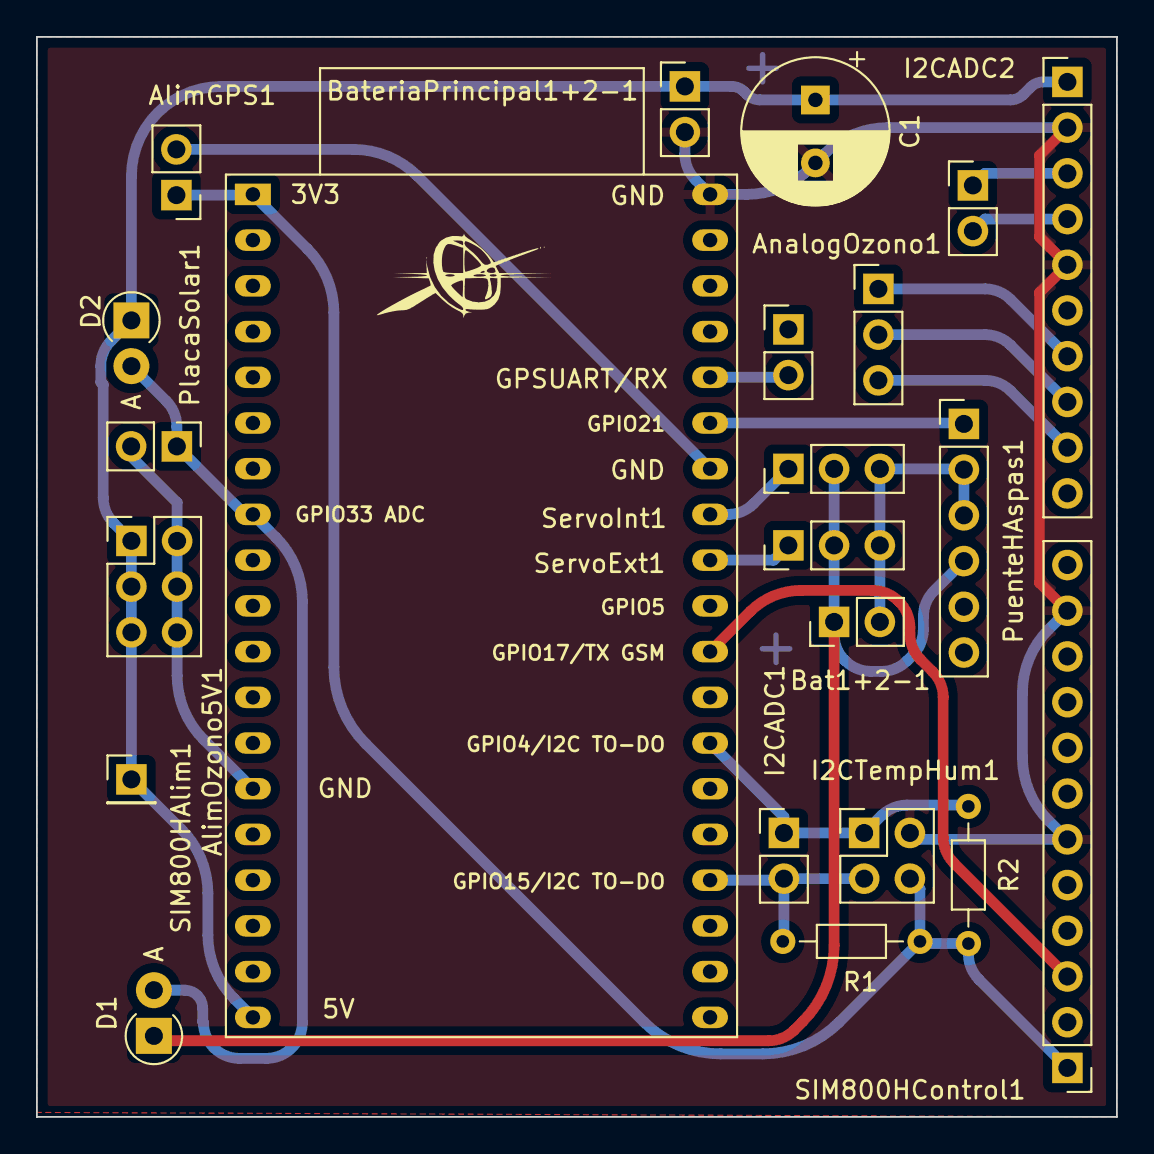
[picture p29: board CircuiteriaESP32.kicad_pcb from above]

Board: 2 copper layers, 60.0 x 60.0 mm, 22 parts (0 on the bottom side), 20 nets.

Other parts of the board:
GPSUART/RX: Conn_01x02; PinHeader_1x02_P2.54mm_Vertical

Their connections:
unnamed 10: GPSUART/RX.2; also elsewhere on the board

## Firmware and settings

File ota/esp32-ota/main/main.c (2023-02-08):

/**
 * @file main.c
 */

#include <string.h>
#include <sys/param.h>
#include <sys/socket.h>

#include "protocol_examples_common.h"

#include "lwip/err.h"
#include "lwip/sockets.h"
#include "lwip/sys.h"
#include "lwip/netdb.h"
#include "lwip/dns.h"

#include "cJSON.h"

#include "mqtt_client.h"

#include "nvs.h"
#include "nvs_flash.h"

#include "freertos/FreeRTOS.h"
#include "freertos/task.h"
#include "esp_system.h"
#include "esp_event.h"
#include "esp_log.h"
#include "esp_ota_ops.h"
#include "esp_http_client.h"
#include "esp_https_ota.h"
#include "string.h"

//Ficheros de nuestro workspace
#include "main.h"
#include "wifi.h"

#define HASH_LEN 32

extern const uint8_t server_cert_pem_start[] asm("_binary_ca_cert_pem_start");
extern const uint8_t server_cert_pem_end[] asm("_binary_ca_cert_pem_end");

/*! Saves bit values used in application */
static EventGroupHandle_t event_group;

/*! Saves OTA config received from ThingsBoard*/
static struct shared_keys
{
    char targetFwServerUrl[256];
    char targetFwVer[128];
} shared_attributes;

/*! Buffer to save a received MQTT message */
static char mqtt_msg[512];

static esp_mqtt_client_handle_t mqtt_client;

extern const uint8_t server_cert_pem_start[] asm("_binary_ca_cert_pem_start");
extern const uint8_t server_cert_pem_end[] asm("_binary_ca_cert_pem_end");

#define OTA_URL_SIZE 256

static void parse_ota_config(const cJSON *object)
{
    if (object != NULL)
    {
        cJSON *server_url_response = cJSON_GetObjectItem(object, TB_SHARED_ATTR_FIELD_TARGET_FW_URL);
        if (cJSON_IsString(server_url_response) && (server_url_response->valuestring != NULL) && strlen(server_url_response->valuestring) < sizeof(shared_attributes.targetFwServerUrl))
        {
            memcpy(shared_attributes.targetFwServerUrl, server_url_response->valuestring, strlen(server_url_response->valuestring));
            shared_attributes.targetFwServerUrl[sizeof(shared_attributes.targetFwServerUrl) - 1] = 0;
            ESP_LOGI(TAG, "Received firmware URL: %s", shared_attributes.targetFwServerUrl);
        }

        cJSON *target_fw_ver_response = cJSON_GetObjectItem(object, TB_SHARED_ATTR_FIELD_TARGET_FW_VER);
        if (cJSON_IsString(target_fw_ver_response) && (target_fw_ver_response->valuestring != NULL) && strlen(target_fw_ver_response->valuestring) < sizeof(shared_attributes.targetFwVer))
        {
            memcpy(shared_attributes.targetFwVer, target_fw_ver_response->valuestring, strlen(target_fw_ver_response->valuestring));
            shared_attributes.targetFwVer[sizeof(shared_attributes.targetFwVer) - 1] = 0;
            ESP_LOGI(TAG, "Received firmware version: %s", shared_attributes.targetFwVer);
        }
    }
}

static esp_err_t mqtt_event_handler(esp_mqtt_event_handle_t event)
{
    assert(event != NULL);

    switch (event->event_id)
    {
    case MQTT_EVENT_CONNECTED:
        xEventGroupClearBits(event_group, MQTT_DISCONNECTED_EVENT);
        xEventGroupSetBits(event_group, MQTT_CONNECTED_EVENT);
        ESP_LOGD(TAG, "MQTT_EVENT_CONNECTED");
        break;
    case MQTT_EVENT_DISCONNECTED:
        xEventGroupClearBits(event_group, MQTT_CONNECTED_EVENT);
        xEventGroupSetBits(event_group, MQTT_DISCONNECTED_EVENT);
        ESP_LOGD(TAG, "MQTT_EVENT_DISCONNECTED");
        break;
    case MQTT_EVENT_SUBSCRIBED:
        ESP_LOGD(TAG, "MQTT_EVENT_SUBSCRIBED, msg_id=%d", event->msg_id);
        break;
    case MQTT_EVENT_UNSUBSCRIBED:
        ESP_LOGD(TAG, "MQTT_EVENT_UNSUBSCRIBED, msg_id=%d", event->msg_id);
        break;
    case MQTT_EVENT_PUBLISHED:
        ESP_LOGD(TAG, "MQTT_EVENT_PUBLISHED, msg_id=%d", event->msg_id);
        break;
    case MQTT_EVENT_DATA:
        ESP_LOGD(TAG, "MQTT_EVENT_DATA, msg_id=%d, %s", event->msg_id, event->topic);
        if (event->data_len >= (sizeof(mqtt_msg) - 1))
        {
            ESP_LOGE(TAG, "Received MQTT message size [%d] more than expected [%d]", event->data_len, (sizeof(mqtt_msg) - 1));
            return ESP_FAIL;
        }

        if (strcmp(TB_ATTRIBUTES_RESPONSE_TOPIC, event->topic) == 0)
        {
            memcpy(mqtt_msg, event->data, event->data_len);
            mqtt_msg[event->data_len] = 0;
            cJSON *attributes = cJSON_Parse(mqtt_msg);
            if (attributes != NULL)
            {
                cJSON *shared = cJSON_GetObjectItem(attributes, "shared");
                parse_ota_config(shared);
            }

            char *attributes_string = cJSON_Print(attributes);
            cJSON_Delete(attributes);
            ESP_LOGD(TAG, "Shared attributes response: %s", attributes_string);
            // Free is intentional, it's client responsibility to free the result of cJSON_Print
            free(attributes_string);
            xEventGroupSetBits(event_group, OTA_CONFIG_FETCHED_EVENT);
        }
        else if (strcmp(TB_ATTRIBUTES_TOPIC, event->topic) == 0)
        {
            memcpy(mqtt_msg, event->data, MIN(event->data_len, sizeof(mqtt_msg)));
            mqtt_msg[event->data_len] = 0;
            cJSON *attributes = cJSON_Parse(mqtt_msg);
            parse_ota_config(attributes);
            char *attributes_string = cJSON_Print(attributes);
            cJSON_Delete(attributes);
            ESP_LOGD(TAG, "Shared attributes were updated on ThingsBoard: %s", attributes_string);
            // Free is intentional, it's client responsibility to free the result of cJSON_Print
            free(attributes_string);
            xEventGroupSetBits(event_group, OTA_CONFIG_UPDATED_EVENT);
        }
        break;
    case MQTT_EVENT_ERROR:
        ESP_LOGD(TAG, "MQTT_EVENT_ERROR");
        break;
    case MQTT_EVENT_BEFORE_CONNECT:
        ESP_LOGD(TAG, "MQTT_EVENT_BEFORE_CONNECT");
        break;
    default:
        ESP_LOGD(TAG, "Other event");
        break;
    }
    return ESP_OK;
}

esp_err_t _http_event_handler(esp_http_client_event_t *evt)
{
    assert(evt != NULL);

    switch (evt->event_id)
    {
    case HTTP_EVENT_ERROR:
        ESP_LOGD(TAG, "HTTP_EVENT_ERROR");
        break;
    case HTTP_EVENT_ON_CONNECTED:
        ESP_LOGD(TAG, "HTTP_EVENT_ON_CONNECTED");
        break;
    case HTTP_EVENT_HEADER_SENT:
        ESP_LOGD(TAG, "HTTP_EVENT_HEADER_SENT");
        break;
    case HTTP_EVENT_ON_HEADER:
        ESP_LOGD(TAG, "HTTP_EVENT_ON_HEADER, key=%s, value=%s", evt->header_key, evt->header_value);
        break;
    case HTTP_EVENT_ON_DATA:
        ESP_LOGD(TAG, "HTTP_EVENT_ON_DATA, len=%d", evt->data_len);
        if (!esp_http_client_is_chunked_response(evt->client))
        {
            // Write out data
            ESP_LOGD(TAG, "%.*s", evt->data_len, (char *)evt->data);
        }
        break;
    case HTTP_EVENT_ON_FINISH:
        ESP_LOGD(TAG, "HTTP_EVENT_ON_FINISH");
        break;
    case HTTP_EVENT_DISCONNECTED:
        ESP_LOGD(TAG, "HTTP_EVENT_DISCONNECTED");
        break;
    default:
        ESP_LOGD(TAG, "Other event");
        break;
    }
    return ESP_OK;
}

/**
 * @brief Main application task, it sends counter value to ThingsBoard telemetry MQTT topic.
 *
 * @param pvParameters Pointer to the task arguments
 */
static void main_application_task(void *pvParameters)
{
    uint8_t counter = 0;

    while (1)
    {
        xEventGroupWaitBits(event_group, OTA_TASK_IN_NORMAL_STATE_EVENT, false, true, portMAX_DELAY);

        counter = counter < 1 ? counter + 1 : 0;

        cJSON *root = cJSON_CreateObject();
        cJSON_AddNumberToObject(root, "counter", counter);
        char *post_data = cJSON_PrintUnformatted(root);
        esp_mqtt_client_publish(mqtt_client, TB_TELEMETRY_TOPIC, post_data, 0, 1, 0);
        cJSON_Delete(root);
        // Free is intentional, it's client responsibility to free the result of cJSON_Print
        free(post_data);

        vTaskDelay(1000 / portTICK_PERIOD_MS);
    }
}

/**
 * @brief Check is the current running partition label is factory
 *
 * @param running_partition_label Current running partition label
 * @param config_name Configuration name that specified in Kconfig, ThingsBoard OTA configuration submenu
 * @return true If current running partition label is 'factory'
 * @return false If current runnit partition label is not 'factory'
 */
static bool partition_is_factory(const char *running_partition_label, const char *config_name)
{
    if (strcmp(FACTORY_PARTITION_LABEL, running_partition_label) == 0)
    {
        ESP_LOGW(TAG, "Factory partition is running. %s from config is saving to the flash memory", config_name);
        return true;
    }
    else
    {
        ESP_LOGE(TAG, "%s wasn't found, running partition is not '%s'", config_name, FACTORY_PARTITION_LABEL);
        APP_ABORT_ON_ERROR(ESP_FAIL);
        return false;
    }
}

/**
 * @brief Get MQTT broker URL to use in MQTT client.
 *        If the flash memory is empty and running partition is 'factory'
 *        then MQTT broker URL specified in ThingsBoard OTA configuration submenu will be saved to NVS.
 *        If running partition is not 'factory' ('ota_0' or 'ota_1') then MQTT broker URL from NVS is used.
 *        The application stops if running partition is not 'factory' and MQTT broker URL was not found in NVS.
 *
 * @param running_partition_label Current running partition label
 * @return const char* MQTT broker URL
 */
static const char *get_mqtt_url(const char *running_partition_label)
{
    nvs_handle handle;
    APP_ABORT_ON_ERROR(nvs_open(NVS_KEY_MQTT_URL, NVS_READWRITE, &handle));

    static char mqtt_url[MAX_LENGTH_TB_URL + 1];
    size_t mqtt_url_len = sizeof(mqtt_url);

    esp_err_t result_code = nvs_get_str(handle, NVS_KEY_MQTT_URL, mqtt_url, &mqtt_url_len);
    if (result_code == ESP_OK)
    {
        ESP_LOGI(TAG, "MQTT URL from flash memory: %s", mqtt_url);
    }
    else if (result_code == ESP_ERR_NVS_NOT_FOUND)
    {
        if (partition_is_factory(running_partition_label, "MQTT URL"))
        {
            APP_ABORT_ON_ERROR(nvs_set_str(handle, NVS_KEY_MQTT_URL, CONFIG_MQTT_BROKER_URL));
            APP_ABORT_ON_ERROR(nvs_commit(handle));
            APP_ABORT_ON_ERROR(nvs_get_str(handle, NVS_KEY_MQTT_URL, mqtt_url, &mqtt_url_len));
        }
    }
    else
    {
        ESP_LOGE(TAG, "Unable to to get MQTT URL from NVS");
        APP_ABORT_ON_ERROR(ESP_FAIL);
    }

    nvs_close(handle);
    return mqtt_url;
}

/**
 * @brief Get MQTT broker port to use in MQTT client.
 *        If the flash memory is empty and running partition is 'factory'
 *        then MQTT broker port specified in ThingsBoard OTA configuration submenu will be saved to NVS.
 *        If running partition is not 'factory' ('ota_0' or 'ota_1') then MQTT broker port from NVS is used.
 *        The application stops if running partition is not 'factory' and MQTT broker port was not found in NVS.
 *
 * @param running_partition_label Current running partition label
 * @return const char* MQTT broker port
 */
static uint32_t get_mqtt_port(const char *running_partition_label)
{
    nvs_handle handle;
    APP_ABORT_ON_ERROR(nvs_open(NVS_KEY_MQTT_PORT, NVS_READWRITE, &handle));

    uint32_t mqtt_port;

    esp_err_t result_code = nvs_get_u32(handle, NVS_KEY_MQTT_PORT, &mqtt_port);
    if (result_code == ESP_OK)
    {
        ESP_LOGI(TAG, "MQTT port from flash memory: %d", mqtt_port);
    }
    else if (result_code == ESP_ERR_NVS_NOT_FOUND)
    {
        if (partition_is_factory(running_partition_label, "MQTT port"))
        {
            APP_ABORT_ON_ERROR(nvs_set_u32(handle, NVS_KEY_MQTT_PORT, CONFIG_MQTT_BROKER_PORT));
            APP_ABORT_ON_ERROR(nvs_commit(handle));
            APP_ABORT_ON_ERROR(nvs_get_u32(handle, NVS_KEY_MQTT_PORT, &mqtt_port));
        }
    }
    else
    {
        ESP_LOGE(TAG, "Unable to to get MQTT port from NVS");
        APP_ABORT_ON_ERROR(ESP_FAIL);
    }

    nvs_close(handle);
    return mqtt_port;
}

/**
 * @brief Get MQTT access token to use in MQTT client.
 *        If the flash memory is empty and running partition is 'factory'
 *        then MQTT broker access token specified in ThingsBoard OTA configuration submenu will be saved to NVS.
 *        If running partition is not 'factory' ('ota_0' or 'ota_1') then MQTT broker access token from NVS is used.
 *        The application stops if running partition is not 'factory' and MQTT broker access token was not found in NVS.
 *
 * @param running_partition_label Current running partition label
 * @return const char* MQTT broker access token
 */
static const char *get_mqtt_access_token(const char *running_partition_label)
{
    nvs_handle handle;
    APP_ABORT_ON_ERROR(nvs_open(NVS_KEY_MQTT_ACCESS_TOKEN, NVS_READWRITE, &handle));

    static char access_token[MAX_LENGTH_TB_ACCESS_TOKEN + 1];
    size_t access_token_len = sizeof(access_token);

    esp_err_t result_code = nvs_get_str(handle, NVS_KEY_MQTT_ACCESS_TOKEN, access_token, &access_token_len);
    if (result_code == ESP_OK)
    {
        ESP_LOGI(TAG, "MQTT access token from flash memory: %s", access_token);
    }
    else if (result_code == ESP_ERR_NVS_NOT_FOUND)
    {
        if (partition_is_factory(running_partition_label, "MQTT access token"))
        {
            APP_ABORT_ON_ERROR(nvs_set_str(handle, NVS_KEY_MQTT_ACCESS_TOKEN, CONFIG_MQTT_ACCESS_TOKEN));
            APP_ABORT_ON_ERROR(nvs_commit(handle));
            APP_ABORT_ON_ERROR(nvs_get_str(handle, NVS_KEY_MQTT_ACCESS_TOKEN, access_token, &access_token_len));
        }
    }
    else
    {
        ESP_LOGE(TAG, "Unable to to get MQTT access token from NVS");
        APP_ABORT_ON_ERROR(ESP_FAIL);
    }

    nvs_close(handle);
    return access_token;
}

static void mqtt_app_start(const char *running_partition_label)
{
    assert(running_partition_label != NULL);

    const char *mqtt_url = get_mqtt_url(running_partition_label);
    const uint32_t mqtt_port = get_mqtt_port(running_partition_label);
    const char *mqtt_access_token = get_mqtt_access_token(running_partition_label);

    esp_mqtt_client_config_t mqtt_cfg = {
        .uri = mqtt_url,
        .event_handle = mqtt_event_handler,
        .port = mqtt_port,
        .username = mqtt_access_token};

    mqtt_client = esp_mqtt_client_init(&mqtt_cfg);
    APP_ABORT_ON_ERROR(esp_mqtt_client_start(mqtt_client));

    vTaskDelay(1000 / portTICK_PERIOD_MS);
}

static bool fw_versions_are_equal(const char *current_ver, const char *target_ver)
{
    assert(current_ver != NULL && target_ver != NULL);

    if (strcmp(current_ver, target_ver) == 0)
    {
        ESP_LOGW(TAG, "Skipping OTA, firmware versions are equal - current: %s, target: %s", FIRMWARE_VERSION, shared_attributes.targetFwVer);
        return true;
    }
    return false;
}

static bool ota_params_are_specified(struct shared_keys ota_config)
{
    if (strlen(ota_config.targetFwServerUrl) == 0)
    {
        ESP_LOGW(TAG, "Firmware URL is not specified");
        return false;
    }

    if (strlen(ota_config.targetFwVer) == 0)
    {
        ESP_LOGW(TAG, "Target firmware version is not specified");
        return false;
    }

    return true;
}

static void start_ota(const char *current_ver, struct shared_keys ota_config)
{
    assert(current_ver != NULL);

    if (!fw_versions_are_equal(current_ver, ota_config.targetFwVer) && ota_params_are_specified(ota_config))
    {
        ESP_LOGW(TAG, "Starting OTA, firmware versions are different - current: %s, target: %s", current_ver, ota_config.targetFwVer);
        ESP_LOGI(TAG, "Target firmware version: %s", ota_config.targetFwVer);
        ESP_LOGI(TAG, "Firmware URL: %s", ota_config.targetFwServerUrl);
        esp_http_client_config_t config = {
            .url = ota_config.targetFwServerUrl,
            .cert_pem = (char *)server_cert_pem_start,
            .event_handler = _http_event_handler,
            .keep_alive_enable = true,
#ifdef CONFIG_EXAMPLE_FIRMWARE_UPGRADE_BIND_IF
            .if_name = &ifr,
#endif
        };

#ifdef CONFIG_EXAMPLE_SKIP_COMMON_NAME_CHECK
        config.skip_cert_common_name_check = true;
#endif
        esp_err_t ret = esp_https_ota(&config);
        if (ret == ESP_OK)
        {
            esp_restart();
        }
        else
        {
            ESP_LOGE(TAG, "Firmware Upgrades Failed");
        }
    }
}

static enum state connection_state(BaseType_t actual_event, const char *current_state_name)
{
    assert(current_state_name != NULL);

    if (actual_event & WIFI_DISCONNECTED_EVENT)
    {
        ESP_LOGE(TAG, "%s state, Wi-Fi not connected, wait for the connect", current_state_name);
        return STATE_WAIT_WIFI;
    }

    if (actual_event & MQTT_DISCONNECTED_EVENT)
    {
        ESP_LOGW(TAG, "%s state, MQTT not connected, wait for the connect", current_state_name);
        return STATE_WAIT_MQTT;
    }

    return STATE_CONNECTION_IS_OK;
}
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
void app_main()
{
    event_group = xEventGroupCreate();
    xTaskCreate(&ota_task, "ota_task", 8192, NULL, 5, NULL);
    xTaskCreate(&main_application_task, "main_application_task", 8192, NULL, 5, NULL);
}

void notify_wifi_connected()
{
    xEventGroupClearBits(event_group, WIFI_DISCONNECTED_EVENT);
    xEventGroupSetBits(event_group, WIFI_CONNECTED_EVENT);
}

void notify_wifi_disconnected()
{
    xEventGroupClearBits(event_group, WIFI_CONNECTED_EVENT);
    xEventGroupSetBits(event_group, WIFI_DISCONNECTED_EVENT);
}

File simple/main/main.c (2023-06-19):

/* Simple HTTP + SSL Server Example

   This example code is in the Public Domain (or CC0 licensed, at your option.)

   Unless required by applicable law or agreed to in writing, this
   software is distributed on an "AS IS" BASIS, WITHOUT WARRANTIES OR
   CONDITIONS OF ANY KIND, either express or implied.
*/

#include <esp_wifi.h>
#include <esp_event.h>
#include <esp_log.h>
#include <esp_system.h>
#include <nvs_flash.h>
#include <sys/param.h>
#include "esp_netif.h"
#include "esp_eth.h"
#include "protocol_examples_common.h"

#include <esp_https_server.h>
#include "esp_tls.h"

// Del LED
#include <stdio.h>
#include "driver/gpio.h"
#include "led_strip.h"
#include "sdkconfig.h"
// Fin de includes del LED

/*Del ADC específicamente*/
#include "driver/adc.h"
#include "esp_adc_cal.h"
// Fin de la seccion ADC

// Del reseteo de fabrica
#include "esp_partition.h"
#include "esp_https_ota.h"
#include "esp_ota_ops.h"
#include "esp_log.h"

// MQTT

#include "lwip/sockets.h"
#include "lwip/dns.h"
#include "lwip/netdb.h"

#include "mqtt_client.h"

#include <stdint.h>
#include <stddef.h>
#include "esp_wifi.h"
#include "esp_system.h"
#include "esp_event.h"

#include "freertos/FreeRTOS.h"
#include "freertos/task.h"
#include "freertos/semphr.h"
#include "freertos/queue.h"

// Aniadir libreria cJSON
#include "cJSON.h"

// Para I2C
#include "driver/i2c.h"

#include "driver/spi_master.h"

// Para GPS
#include "nmea_parser.h"

// Para mensajes genéricos
#include <string.h>
#include <math.h>

// Para Telegram
/*
#include <stdlib.h>
#include <sys/time.h>
#include "lwip/apps/sntp.h"

#include "sh2lib.h"
*/

// Para los sleep
/*#include <time.h>
#include "soc/soc_caps.h"
#include "esp_sleep.h"
#include "driver/rtc_io.h"
#include "soc/rtc.h"
#include "esp32/ulp.h"*/
#include "driver/uart.h"

// Para display
#include "ssd1306.h"
//#include "font8x8_basic.h"

// Para motores
#include "driver/mcpwm.h"

/* A simple example made to save the World
 * via a flying balloon vacuum cleaner.
 */

static const char *TAG = "AspiradO3";

xSemaphoreHandle Semaphore;
int enEllo = 0;

/* Motores AspiradO3 */
// Motor Aspirador
#define PIN_ASPIRADOR 21

// Motor interno que redirige hacia adelante o atrás
#define SERVOTIMONINTERNO_MIN_PULSEWIDTH_US (1000) // Minimum pulse width in microsecond
#define SERVOTIMONINTERNO_MAX_PULSEWIDTH_US (2000) // Maximum pulse width in microsecond
#define SERVOTIMONINTERNO_MAX_DEGREE        (45)   // Maximum angle in degree upto which servo can rotate (+-)

// Motor del timón externo que gira de -90 a 90.
#define SERVOTIMONEXTERNO_MIN_PULSEWIDTH_US (600) // Minimum pulse width in microsecond
#define SERVOTIMONEXTERNO_MAX_PULSEWIDTH_US (2600) // Maximum pulse width in microsecond
#define SERVOTIMONEXTERNO_MAX_DEGREE        (90)   // Maximum angle in degree upto which servo can rotate

#define SERVO_PULSE_TIMONINTERNO        (18)   // GPIO connects to the PWM signal line
#define SERVO_PULSE_TIMONEXTERNO        (19)   // GPIO connects to the PWM signal line


/* Sensores ozono */
/* COSAS MATEMÁTICAS Y DE COMPONENTE MISCELÁNEO*/
#define E 2.718281828459
#define RESLDATASHEET 1000000 // La resistencia del datasheet del sensor MQ131 utilizado en el módulo MikroE de detección de ozono
#define RESL 10100 // Va de 100 a 10100 ohmios

#define RESLBABOR 10630 // Lecturas reales del multimetro
#define RESLESTRIBOR 9550
#define RESLTRASFILTRO 9640

#define MQ131_DEFAULT_STABLE_CYCLE 15 //Número de ciclos estables

#define VOLTREF 4.500 // En mV ya que las medidas de ADC las obtenemos en mV. Esto en teoría es vref pero a lo mejor difiere (p.ej 3.3V o 5V), por eso no he puesto VOLTREF vref, además tantos motores drenan
#define VOLTREFDATASHEET 5.000


// I2C nota: hemos elegido el 4 y el 0, puede que de incompatibilidades con otros módulos fuera de ESP32
/*
     GPIO num         RTC GPIO Num
SCL: gpio4  Y gpio2   10 y 12
SDA: gpio0  y MTDO    11 y 13

EN LOS PINES NO PONGAIS DE 6 A 11 QUE ESOS SON DE LA FLASH
*/

#define I2C_MASTER_SCL_IO GPIO_NUM_4  /*!< GPIO number used for I2C master clock */
#define I2C_MASTER_SDA_IO GPIO_NUM_15 /*!< GPIO number used for I2C master data  */
#define I2C_MASTER_NUM I2C_NUM_0      /*!< I2C master i2c port number, the number of i2c peripheral interfaces available will depend on the chip */
#define I2C_MASTER_FREQ_HZ 100000     /*!< I2C master clock frequency */
#define I2C_MASTER_TX_BUF_DISABLE 0   /*!< I2C master doesn't need buffer */
#define I2C_MASTER_RX_BUF_DISABLE 0   /*!< I2C master doesn't need buffer */
#define I2C_MASTER_TIMEOUT_MS 10000

#define TEMPHUM_SENSOR_ADDR 0x44 /*Dir sensor tempHum*/
#define COMANDO_TEMPHUM_MSB 0x24
#define COMANDO_TEMPHUM_LSB 0x16 /*Los comandos de este sensor son de 16 bits, indican el MSB el modo y el LSB la frecuencia, así 0x24 0x16 es modo SIngle Shot con baja repetibilidad*/

#define ADC12C_AADR 0x68 /*Direccion del ADC I2C externo, 4 bits de dir (1101) + 3 de canal + bit r/w, 1101 = 0D  
The I2C address bits (A2, A1, A0 bits) for the MCP3423 and MCP3424 are user configurable and
determined by the logic status of the two external address selection pins on the user’s application board
(Adr0 and Adr1 pins)
Así, si lo pongo Adr0 = Adr1 = LOW => la dirección es 0x68 (que se volvería 0xD0 o 0xD1 al añadir el bit de lectura/escritura)
*/
/*Bit de configuracion es por defecto 1 00 1 00 00 (o sea output no actualizado, canal de selección 1, modo conversión continuo, 12 bits, ganacia x1)*/
#define regADCI2C_paraCanal1 0x90 // 1 00 1 0000
#define regADCI2C_paraCanal2 0xB0 // 1 01 1 0000
#define regADCI2C_paraCanal3 0xD0 // 1 10 1 0000
#define regADCI2C_paraCanal4 0xF0 // 1 11 1 0000

/*Basado en https://www.electronicaembajadores.com/Datos/pdf1/sm/smci/ads1015.pdf */
#define ADCI2CADAFRUIT_AADR 0x48 /* La dirección puede ser 1001000 si a GND y 1001001 si conectado pin A0 a VCC */
#define ADCI2CADAFRUIT_CONFIGADDR 0x01 /* La dir del reg de configuracion */
#define ADCI2CADAFRUIT_CONFIGMSB 0x04 /* 0b00000100 MSB of the Config register */
#define ADCI2CADAFRUIT_CONFIGLSB 0x83 /* 0b10000011 LSB of the Config register */
#define ADCI2CADAFRUIT_CONVADDR 0X00 /* 0b00000000 registro de la conversión */
#define ADCI2CADAFRUIT_CONFIGREGMUXA0 0x42 /* Las 4 posibles salidas del ADC */
#define ADCI2CADAFRUIT_CONFIGREGMUXA1 0x52
#define ADCI2CADAFRUIT_CONFIGREGMUXA2 0x62
#define ADCI2CADAFRUIT_CONFIGREGMUXA3 0x72
/* primero hay un 0 de estado operativo, 100 es analog 0 y AInn = GND
101 es AN1
110 es AN2
111 es AN3
Luego 001 para +-4.096 V, 0 para modo continuo, 100 para 1600 SPS, luego 0 0 0 11 para otras opciones por defecto
Por lo tanto tenemos
01000010 10000011
01010010 10000011
01100010 10000011
01110010 10000011
*/

#define LUZ_SENSOR_ADDR 0x10 /*Dir sensor luminosidad*/
#define LUZ_REG_ADDR 0x04    /*Dir registro de luminosidad es 0x04*/

#define MPU9250_PWR_MGMT_1_REG_ADDR 0x6B /*!< Register addresses of the power managment register */
#define MPU9250_RESET_BIT 7
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

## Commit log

2023-02-08 Arreglos al código para ver si funcionaría con motores
    [main.c]
2023-02-13 Added some ozone sensor thing + suggesting a gps library for later
2023-02-13 Aniadido posible codigo para ozono remesas
2023-02-14 kicad parte 1
    [CircuiteriaESP32.kicad_pcb, CircuiteriaESP32.kicad_sch, Esquematicos.kicad_pcb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]
2023-02-16 Mejoras en el disenio kicad y más código generado
    [CircuiteriaESP32.kicad_sch]
2023-02-20 código de GPS
    [Chasis.FCStd]
2023-02-22 Ajustadas algunas cosas, to-do
    [CircuiteriaESP32.kicad_sch]
2023-02-23 Sensores ozono funcionan
2023-03-06 Añadido codigo para adafruit i2c
    [CircuiteriaESP32.kicad_sch]
2023-03-08 Prueba i2c nuevo
2023-03-08 Esquematico actualizado
    [CircuiteriaESP32.kicad_sch]
2023-03-09 Arreglos para servos y algo de sensores
    [CircuiteriaESP32.kicad_sch]
2023-03-15 Actualización motores
    [CircuiteriaESP32.kicad_sch]
2023-03-16 16 de marzo 2023
2023-03-23 23 Marzo 2023
    [CircuiteriaESP32.kicad_sch]
2023-03-27 27 marzo 2023, comienzo de desarrollo de un SC, preguntaré más tarde al profesor Norberto
2023-03-29 Arreglos de antes de Semana Santa
    [main.c]
2023-04-11 Arreglos sensores 11 abril 2023
    [main.c]
2023-04-17 Arreglos 17 abril 2023
    [main.c]
2023-04-18 18 abril 2023
    [CircuiteriaESP32.kicad_sch]
2023-05-01 arreglillos 1 de mayo 2023
    [main.c]
2023-05-04 4 de Mayo 2023
    [CircuiteriaESP32.kicad_sch]
2023-05-08 Lunes 8 Mayo 2023
    [CircuiteriaESP32.kicad_pcb, CircuiteriaESP32.kicad_sch]
2023-05-09 9 mayo 2023
    [CircuiteriaESP32.kicad_pcb, CircuiteriaESP32.kicad_sch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]
2023-05-10 10 mayo 2023
    [CircuiteriaESP32.kicad_pcb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]
2023-05-11 11 de Mayo de 2023
    [CircuiteriaESP32-B_Cu.gbr, CircuiteriaESP32-Edge_Cuts.gbr, CircuiteriaESP32-F_Cu.gbr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]
2023-05-15 15 de mayo 2023
    [CircuiteriaESP32.kicad_pcb]
2023-05-16 16 mayo 2023
    [Chasis.FCStd, Chasis.stl]
2023-05-17 17 mayo 2023
    [ASX1_ChasisMisc.3mf, Chasis-PrincipalBackD.stl, Chasis-PrincipalBackI.stl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]
2023-05-18 18 mayo 2023
    [ASX1_Chasis-PrincipalBackD.3mf, ASX1_Chasis-PrincipalBackI.3mf, ASX1_Chasis-PrincipalFI.3mf]
2023-05-22 22 de mayo 2023
2023-05-23 Arreglos en limpieza de código
    [main.c]
2023-05-23 Arreglos en limpieza de código 2
    [main.c]
2023-05-24 24 mayo 2023
    [ASX1_Chasis-PrincipalBDreajustado.3mf, ASX1_Chasis-PrincipalBIreajustado.3mf, ASX1_Chasis-PrincipalFDRecalculado.3mf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]
2023-05-25 25 mayo 2023
    [ASX1_Chasis-PrincipalBDreajustado.3mf, ASX1_Chasis-PrincipalBIreajustado.3mf, ASX1_Chasis-PrincipalFDRecalculado.3mf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]
2023-05-31 31 de mayo 2023
2023-06-01 1 de Junio 2023
2023-06-16 16 de junio 2023
2023-07-05 5 julio 2023
    [ASX1_soporte_main_structure.3mf, ASX1_soporte_pinzas_tuercas.3mf, main_structure.3mf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]
2023-07-07 7 de julio 2023
2023-07-11 11 de Julio 2023
    [Soporte-MicroEspacioEntrepinzas.stl, Soporte-MicroespacioEntrepinzas.FCStd]
2023-07-13 13 julio 2023 parte II
    [ChasisV2FD.stl, ChasisV2FI.stl, ChasisV2TD.stl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]
2023-09-14 14 Septiembre 2023, reducción aún mayor de peso
    [ChasisBD-v3pto1.stl, ChasisBI-v3pto1.stl, ChasisFD-v3pto1.stl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]
2023-09-19 18 y 19 Septiembre 2023
    [ChasisBD_v3pto2-PROPUESTA.stl, ChasisBI_v3pto2-PROPUESTA.stl]
2023-09-25 25 de Septiembre de 2023 parte 2
2023-09-29 29 Septiembre 2023
    [These_nuts_4.3mf]
2023-10-02 2 de octubre de 2023
    [ASX1_Cuerpo17AbrazaderasSoporte.3mf, Cuerpo17.3mf]
2023-10-03 3 octubre 2023
    [helize.3mf]
2023-10-09 9 de Octubre de 2023
2023-11-16 16 noviembre 2023
    [CE3E3V2_Unnamed-Cubo5-PruebaEnder.3mf, Unnamed-Cubo-PruebaEnder.stl, chasis.3mf]
2023-11-17 17 noviembre 2023
    [CE3E3V2_chasis.3mf]
2023-11-24 24 noviembre 2023
    [CE3E3V2_tapa-trasera.3mf, CE3E3V2_tapas1y2.3mf, CE3E3V2_timon_2.3mf]
2023-12-19 Añadidas imágenes adicionales a la memoria a 19 de diciembre de 2023
2024-01-17 Version 5 de memoria lista
2024-02-01 Version 7.2 de la memoria
2024-02-01 Actualización del índice de la versión 7
